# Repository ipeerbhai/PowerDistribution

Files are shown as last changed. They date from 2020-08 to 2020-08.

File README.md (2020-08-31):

# PowerDistribution
This design is for a small wiring board to provide power to a robotic rover.

It's designed in 3 sections.

## Part 1: High Current ESC Pads ##
This part is 3 thick traces without masking to push high voltage/current power in a short segment.  It is completely unfused, and should be pushed to a smart, power-hungry board like an ODrive.  The lack of masks is to enable solder as a wire for high-current and voltage use cases.

## Part 2: Battery Monitoring ##
This part has 2 SMD resistors in a simple voltage divider circuit.  The resistor values chosen are 22M-ohm (RMCF0805FT22M0) and 1M-ohm(RC0805FR-071ML.  This enables voltage detection on a Teensy 4.1 from 0 to 50V.

## Part 3: Switch and buck converters ##
A large swtich pad for a single pole, single throw switch,
a small pad buck converter for a raspberry pi or other SBC, and 2 large pads for very high-current buck converters for Star-power servos.
For the switch, Amazon part number: B078KBC5VH
For the RPi Buck converter, Amazon part number: B079N9BFZC
For the Star-Power converter, Amazon part number: B0819Y8PJZ

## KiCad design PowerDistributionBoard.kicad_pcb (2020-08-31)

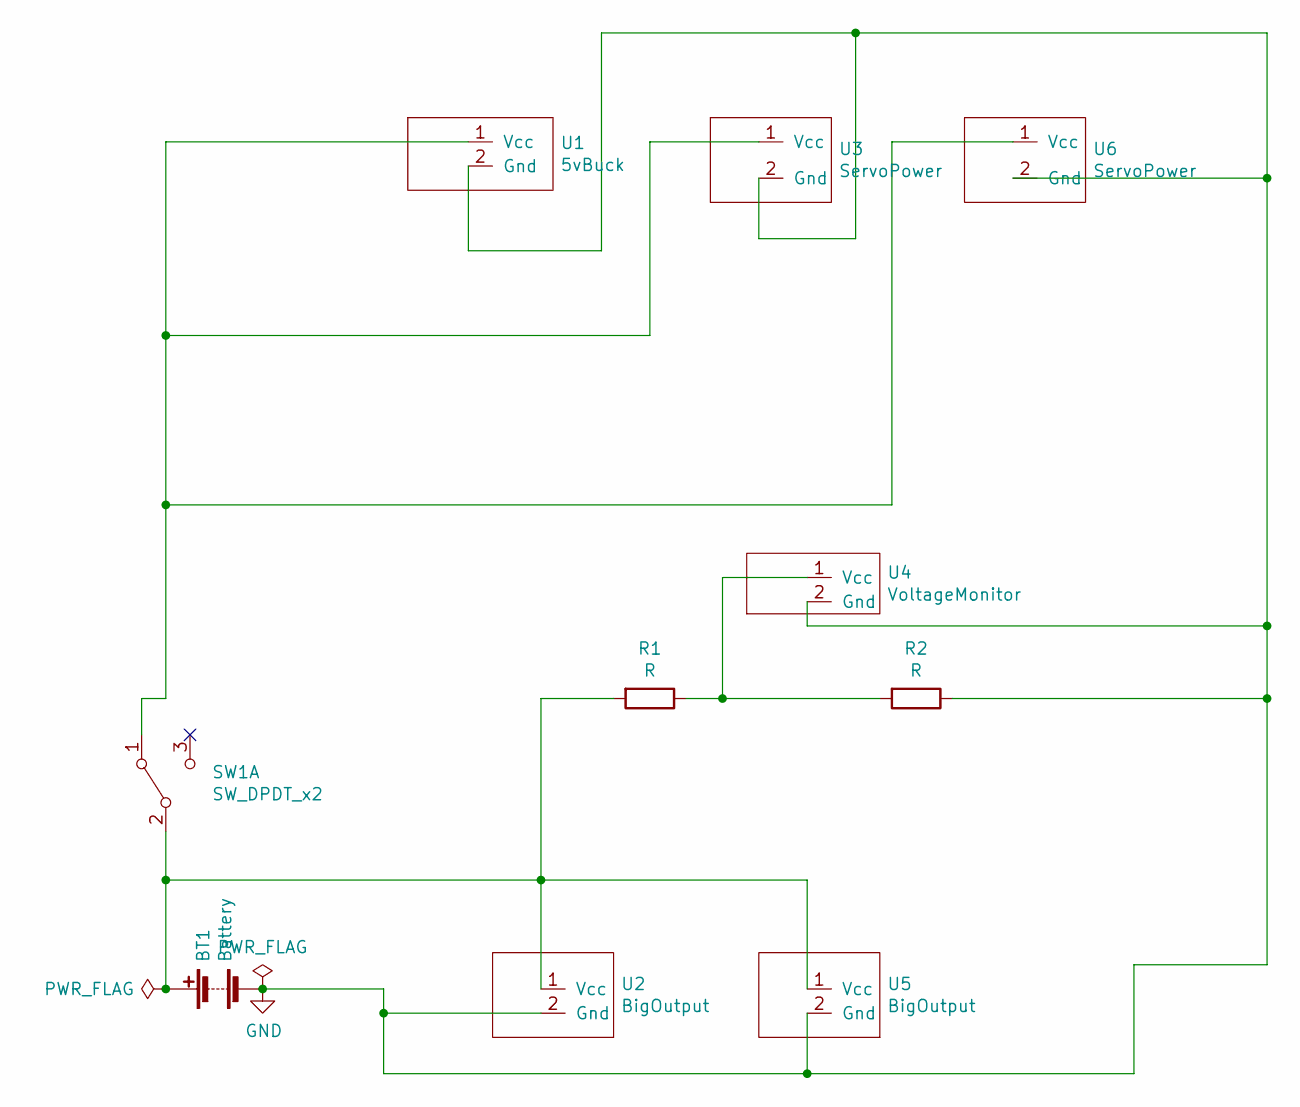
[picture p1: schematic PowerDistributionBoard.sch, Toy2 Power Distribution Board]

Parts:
BT1: Battery; BigOutput
R1, R2: R; R_0805_2012Metric_Pad1.15x1.40mm_HandSolder
SW1: SW_DPDT_x2; BigSwitch
U1: 5vBuck; SmallPower
U2, U5: BigOutput
U3, U6: ServoPower; BigOutput
U4: VoltageMonitor; PinHeader_1x02_P2.54mm_Vertical

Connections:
GND: BT1.2 (-), R2.1, U1.2 (Gnd), U2.2 (Gnd), U3.2 (Gnd), U4.2 (Gnd), U5.2 (Gnd), U6.2 (Gnd)
unnamed: BT1.1 (+), R1.2, SW1.2 (B), U2.1 (Vcc), U5.1 (Vcc)
unnamed: R1.1, R2.2, U4.1 (Vcc)
unnamed: SW1.1 (A), U1.1 (Vcc), U3.1 (Vcc), U6.1 (Vcc)

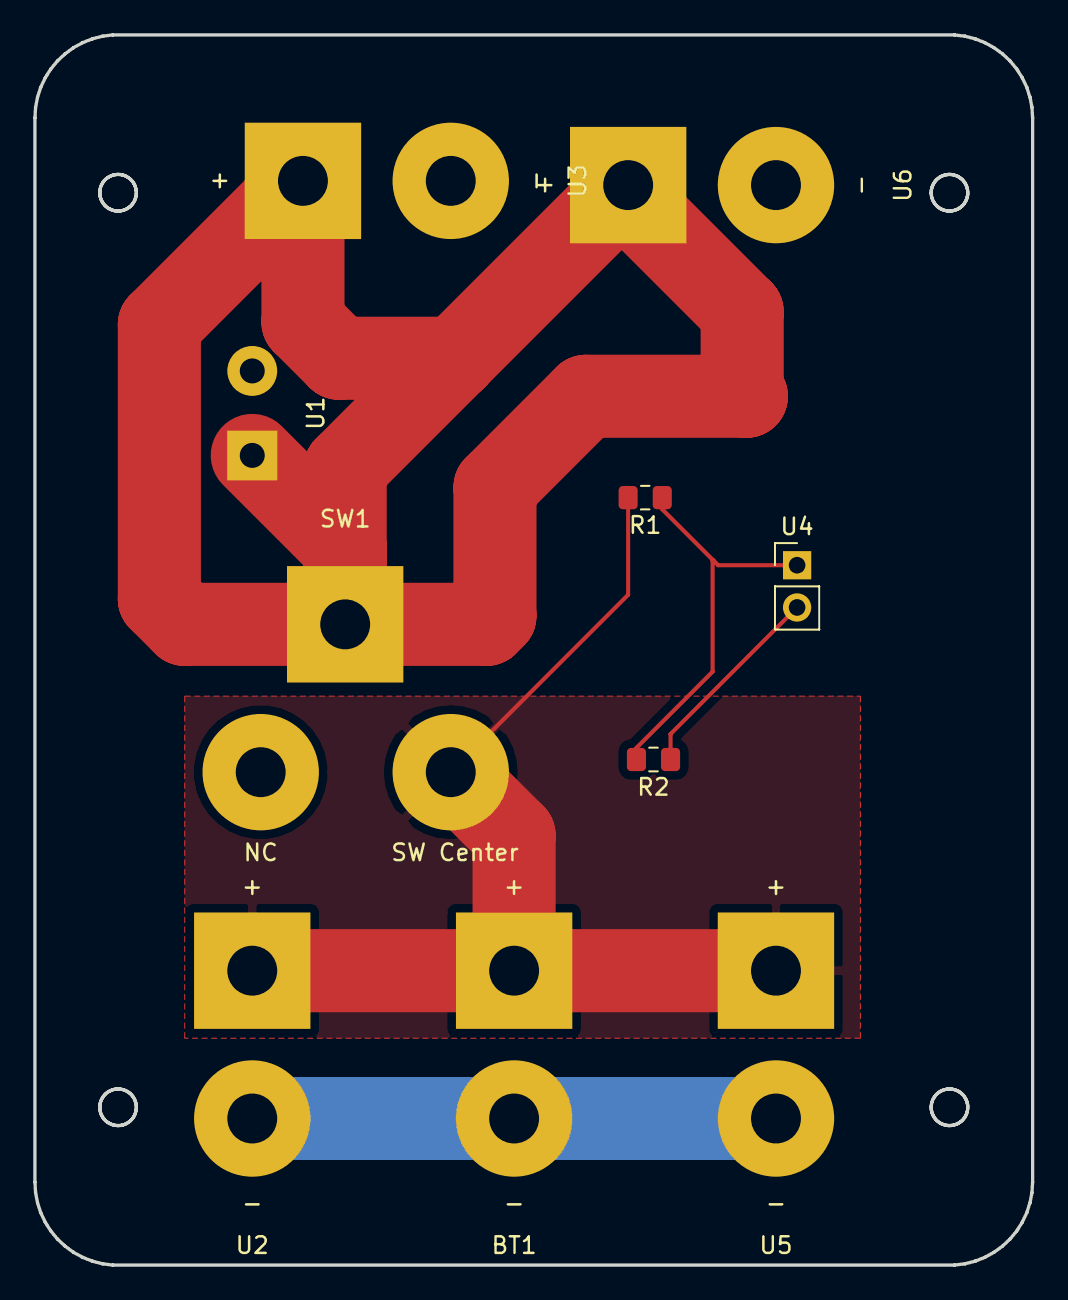
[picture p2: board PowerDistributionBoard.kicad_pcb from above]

Board: 2 copper layers, 60.0 x 74.0 mm, 10 parts (0 on the bottom side), 4 nets.
